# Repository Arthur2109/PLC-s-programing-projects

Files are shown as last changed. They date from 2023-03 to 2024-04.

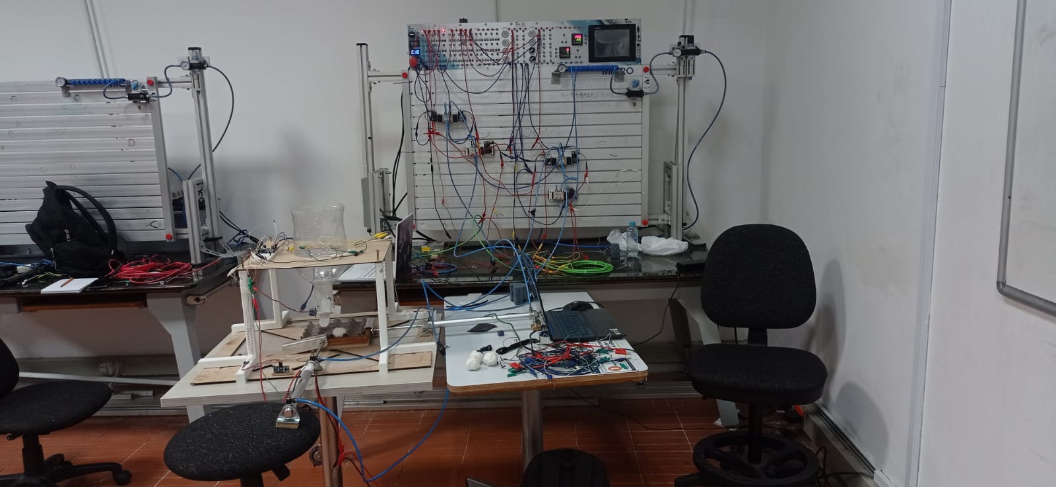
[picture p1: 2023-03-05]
projet-préhenseur-oeuf/photos-vidéos/systeme-entier.jpeg

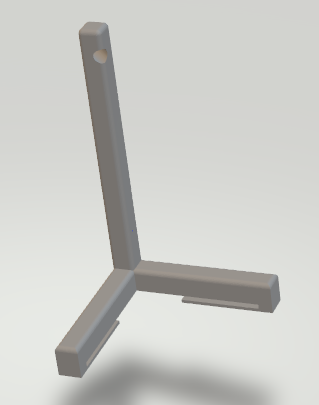
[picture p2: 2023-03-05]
projet-préhenseur-oeuf/trepied/trepied.png

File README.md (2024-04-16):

# PLC-s-programing-projects
PLC's programing projects coded in Ladder, Grafcet or FBD (function block diagram).

1) Projet préhenseur d'oeuf (codé en FDB): projet de plusieurs mois qui consiste a placer des oeufs dans une boite d'oeufs de maniere automatique.
Les oeufs sont a l'origine placés dans une bouteilles (cf photos et vidéos). Un tourniquet s'actionne pour laisser tomber un oeuf dans la boite. A chaque fois qu'un oeuf tombe pour occuper un espace de la boite, les pistons X et Y de déplacent d'un cran (asservissement de la position a l'aide de capteur ultrasons placés le long des axes X et Y, + structure en glissiere qui permet le mouvement independant X Y de la boite). Le parcours de tous les emplacements de la boite est ainsi fait qu'il permet de ne faire aucun aller retour pour ne pas perdre de temps (zig-zag).

Conception des pieces sous Inventor (AutoCAD).

Problemes de ce projet :
- Le capteur ultrason est adapté a un microcontroleur mais pas a un PLC (cf explication fichier arduino).
- La structure des glissieres crée un arc-boutement important et bloque le glissement (cf videos).
- Manque de temps significatif.

2) Grafcet : Petit programme de simulation de deux pistons et d'un moteur codé en Grafcet. Asservissement de la vitesse du moteur. A executer sous Automation Studio.

3) Ladder : Petit programme de simulation de deux pistons, codé en Ladder. le bouton ON actionne les pistons suivant la séquence X+,attente,X-,Y+,attente,Y-. A executer aussi sous Automation Studio.

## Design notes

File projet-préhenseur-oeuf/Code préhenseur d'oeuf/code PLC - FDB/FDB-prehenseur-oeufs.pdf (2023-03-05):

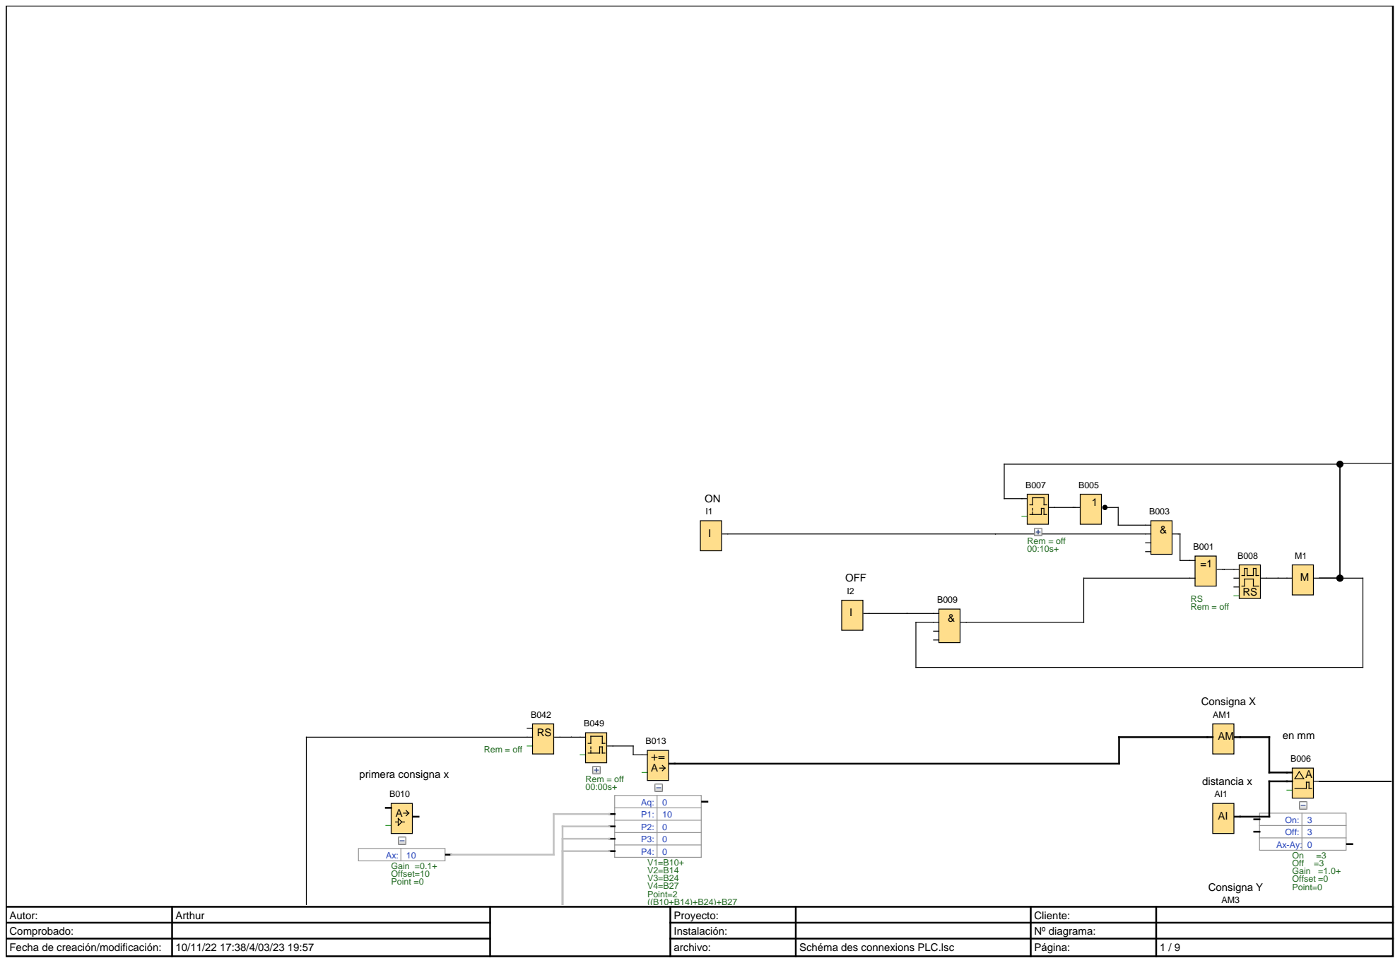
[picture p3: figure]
Autor:; Arthur; Proyecto:; Cliente:; Comprobado:; Instalación:; Nº diagrama:; Fecha de creación/modificación:; archivo:; Schéma des connexions PLC.lsc; OFF; distancia x; Consigna X; Rem = off 00:10s+; Off:; RSRem = off; Consigna Y; V1=B10+ V2=B14 V3=B24 V4=B27 Point=2; Gain =0.1+ Offset=10 Point =0; primera consigna x; Rem = off; Rem = off 00:00s+

On =3 Off =3 Gain =1.0+ Offset =0 Point=0

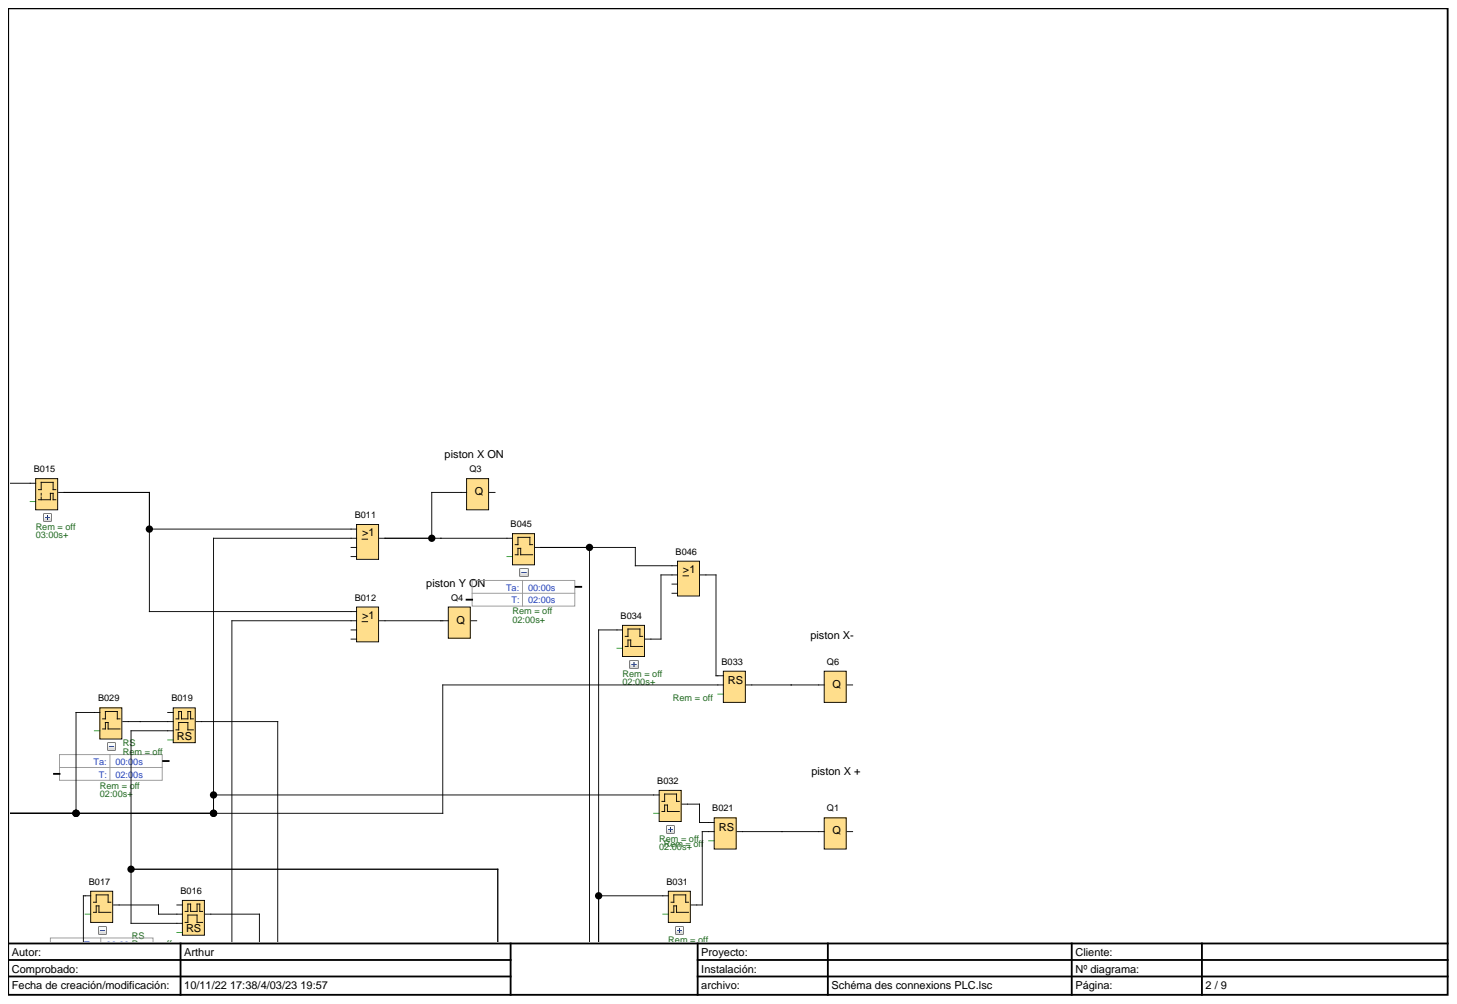
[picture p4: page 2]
piston X ON; piston Y ON; RSRem = off; Rem = off 02:00s+; piston X +; piston X-; Rem = off; Rem = off 03:00s+

Ta: | 00:00s
T: | 02:00s

Autor: | Arthur | Proyecto: | Cliente:

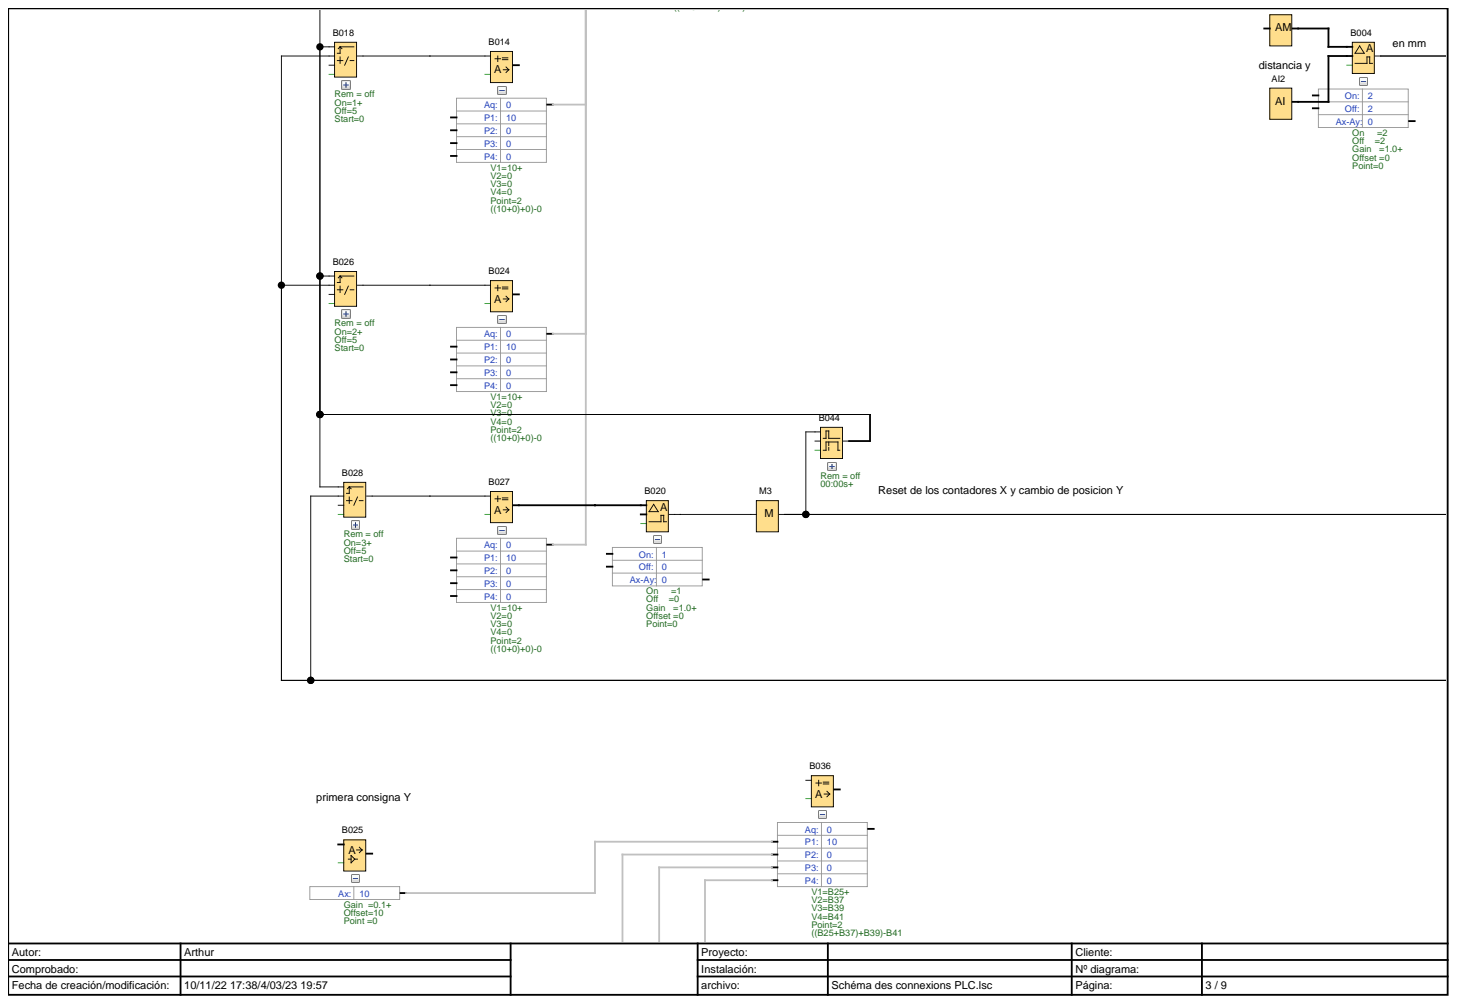
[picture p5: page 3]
Autor:; Arthur; Proyecto:; Cliente:; distancia y; Off:; V1=10+ V2=0 V3=0 V4=0 Point=2; Reset de los contadores X y cambio de posicion Y; primera consigna Y; V1=B25+ V2=B37 V3=B39 V4=B41 Point=2; Rem = off 00:00s+

Rem = off On=1+ Off=5 Start=0

On =2 Off =2 Gain =1.0+ Offset =0 Point=0

P2: | 0
P3: | 0
P4: | 0

Rem = off On=2+ Off=5 Start=0

Aq: | 0
P1: | 10

Rem = off On=3+ Off=5 Start=0

On =1 Off =0 Gain =1.0+ Offset =0 Point=0

Gain =0.1+ Offset=10 Point =0

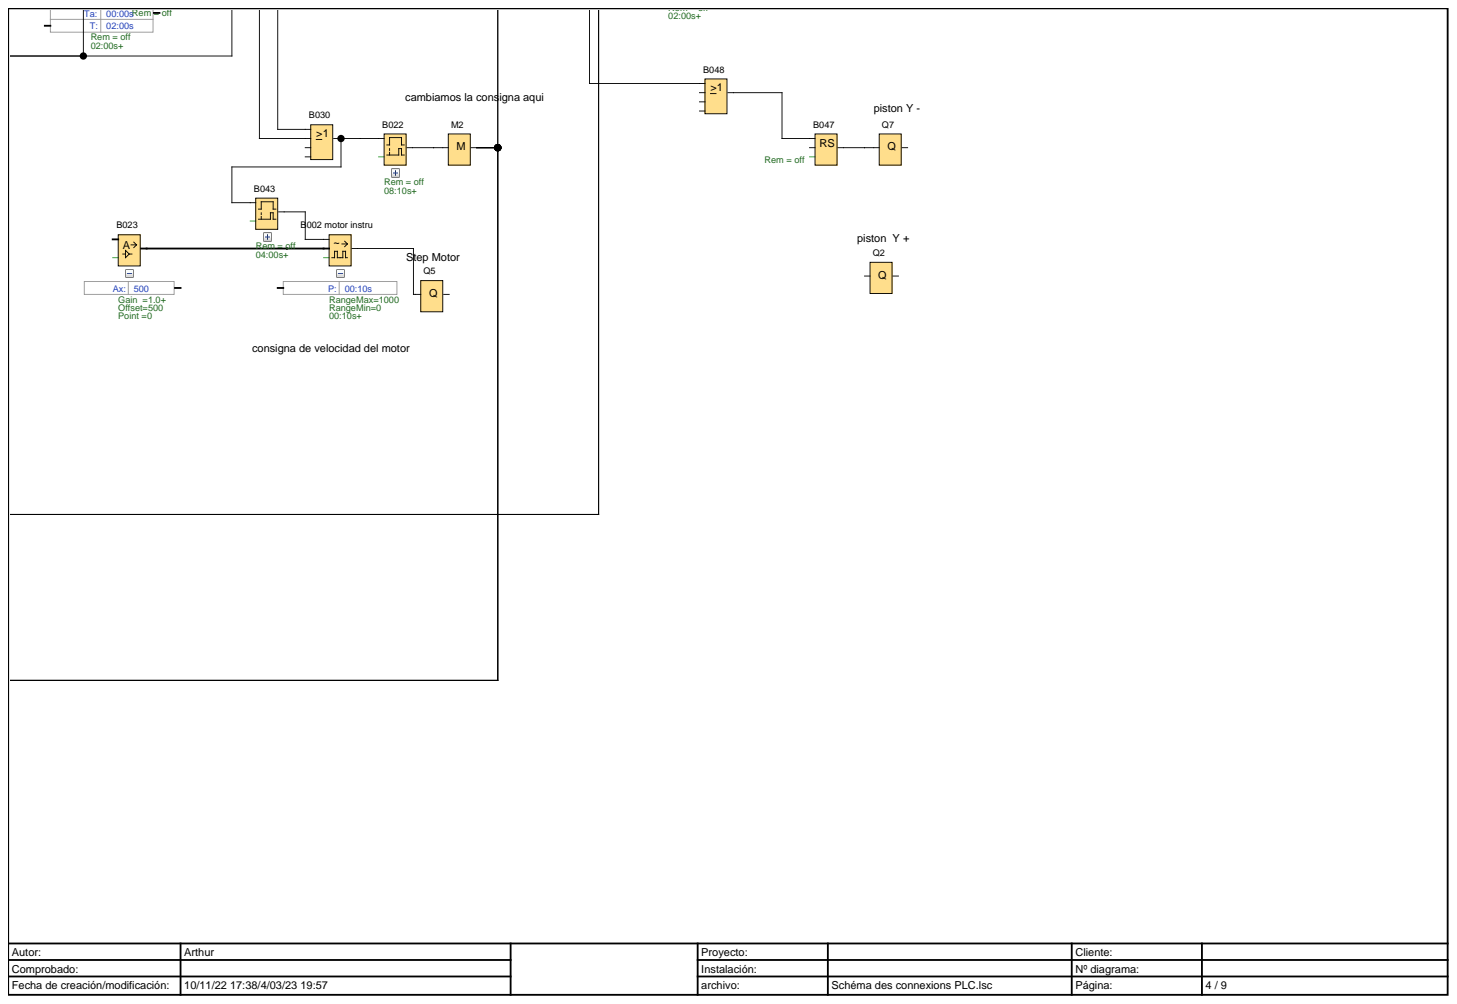
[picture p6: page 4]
Autor:; Arthur; Proyecto:; Cliente:; piston Y + ~; B002 motor instru; RangeMax=1000 RangeMin=0; Step Motor; Rem = off 08:10s+; piston Y -; Rem = off 02:00s+; Rem = off; Rem = off 04:00s+

Ta: | 00:00s Rem = off | B030 | 02:00s+ B048
T: | 02:00s

cambiamos la consigna aqui

Gain =1.0+ Offset=500 Point =0

consigna de velocidad del motor

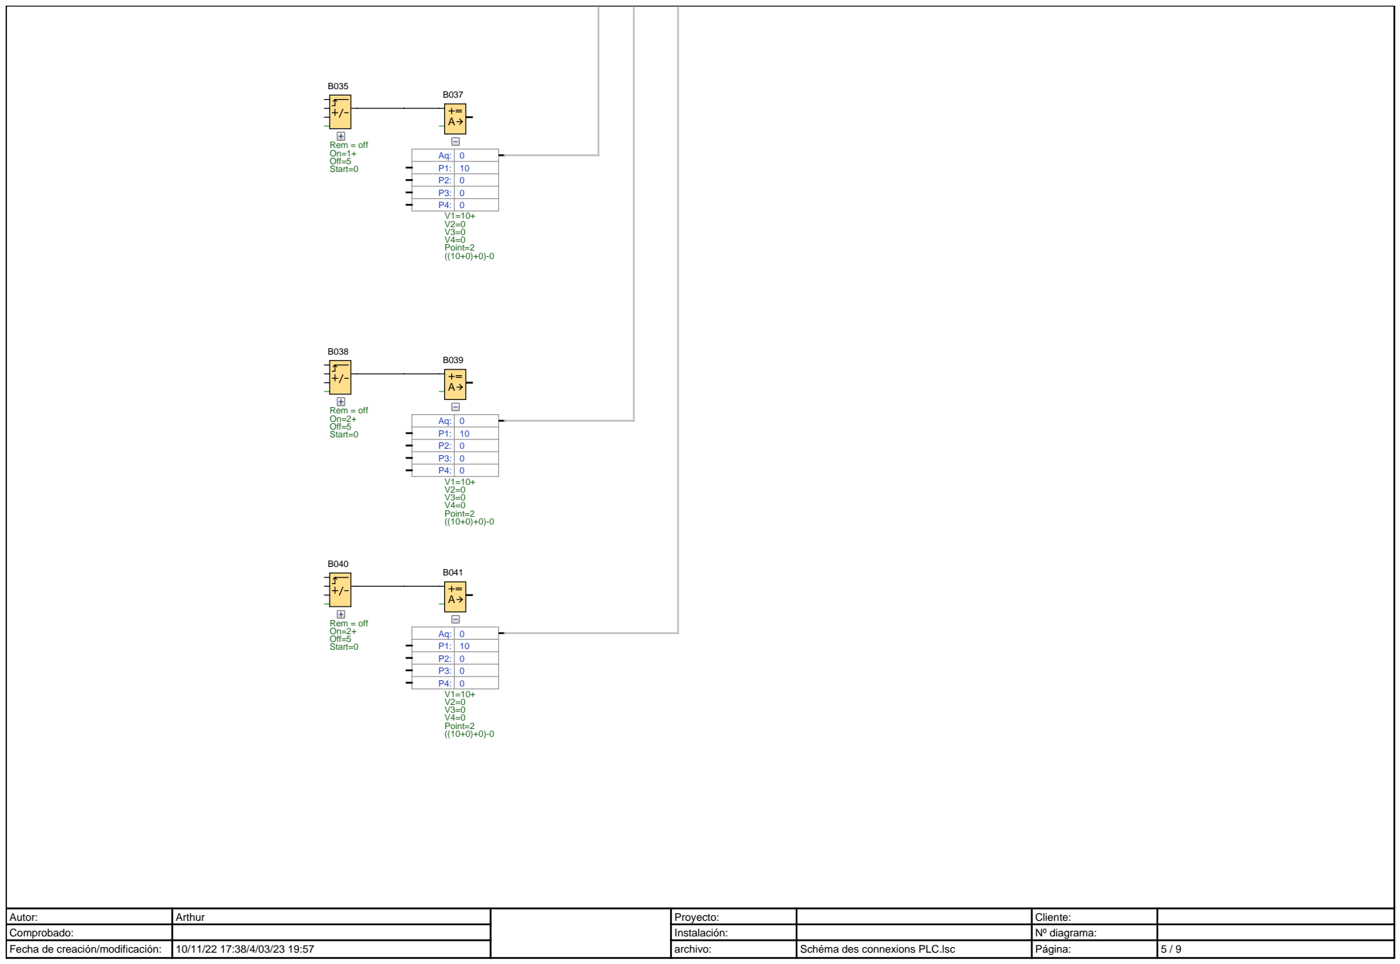
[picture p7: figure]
Autor:; Arthur; Proyecto:; Cliente:; Rem = off On=1+ Off=5 Start=0; V1=10+ V2=0 V3=0 V4=0 Point=2; Rem = off On=2+ Off=5 Start=0

Número de bloque (tipo) | Parámetro

AI1(Entrada analógica) : distancia x

AI2(Entrada analógica) : distancia y

AM1(Marca analógica) : Consigna X

AM3(Marca analógica) : Consigna Y

B002 motor instru(PWM) : | RangeMax=1000 RangeMin=0 00:10s+
B004(Comparador analógico) : | On =2 Off =2 Gain =1.0+ Offset =0 Point=0
B006(Comparador analógico) : | On =3 Off =3 Gain =1.0+ Offset =0 Point=0
B007(Retardo a la conexión) : | Rem = off 00:10s+
B008(Relé de impulsos) : | RS Rem = off
B010(Amplificador analógico) : | Gain =0.1+ Offset=10 Point =0
B013(Instrucción aritmética) : | V1=B10+ V2=B14 V3=B24 V4=B27 Point=2 ((B10+B14)+B24)+B27
B014(Instrucción aritmética) : | V1=10+ V2=0 V3=0 V4=0 Point=2 ((10+0)+0)-0
B015(Retardo a la conexión) : | Rem = off 03:00s+
B016(Relé de impulsos) : | RS Rem = off
B017(Relé de barrido (Salida de impulsos)) : | Rem = off 02:00s+
B018(Contador adelante/atrás) : | Rem = off On=1+ Off=5 Start=0
B019(Relé de impulsos) : | RS Rem = off
B020(Comparador analógico) : | On =1 Off =0 Gain =1.0+ Offset =0 Point=0
B021(Relé autoenclavador) : | Rem = off
B022(Retardo a la conexión) : | Rem = off 08:10s+
B023(Amplificador analógico) : | Gain =1.0+ Offset=500 Point =0
Autor: | Arthur

Proyecto:

Cliente:

Página:

Número de bloque (tipo) | Parámetro
B024(Instrucción aritmética) : | V1=10+ V2=0 V3=0 V4=0 Point=2 ((10+0)+0)-0
B025(Amplificador analógico) : | Gain =0.1+ Offset=10 Point =0
B026(Contador adelante/atrás) : | Rem = off On=2+ Off=5 Start=0
B027(Instrucción aritmética) : | V1=10+ V2=0 V3=0 V4=0 Point=2 ((10+0)+0)-0
B028(Contador adelante/atrás) : | Rem = off On=3+ Off=5 Start=0
B029(Relé de barrido (Salida de impulsos)) : | Rem = off 02:00s+
B031(Relé de barrido (Salida de impulsos)) : | Rem = off 02:00s+
B032(Relé de barrido (Salida de impulsos)) : | Rem = off 02:00s+
B033(Relé autoenclavador) : | Rem = off
B034(Relé de barrido (Salida de impulsos)) : | Rem = off 02:00s+
B035(Contador adelante/atrás) : | Rem = off On=1+ Off=5 Start=0
B036(Instrucción aritmética) : | V1=B25+ V2=B37 V3=B39 V4=B41 Point=2 ((B25+B37)+B39)-B41
B037(Instrucción aritmética) : | V1=10+ V2=0 V3=0 V4=0 Point=2 ((10+0)+0)-0
B038(Contador adelante/atrás) : | Rem = off On=2+ Off=5 Start=0
B039(Instrucción aritmética) : | V1=10+ V2=0 V3=0 V4=0 Point=2 ((10+0)+0)-0
B040(Contador adelante/atrás) : | Rem = off On=2+ Off=5 Start=0
B041(Instrucción aritmética) : | V1=10+ V2=0 V3=0 V4=0 Point=2 ((10+0)+0)-0
B042(Relé autoenclavador) : | Rem = off

Número de bloque (tipo) | Parámetro
B043(Retardo a la conexión) : | Rem = off 04:00s+
B044(Retardo a la desconexión) : | Rem = off 00:00s+
B045(Relé de barrido (Salida de impulsos)) : | Rem = off 02:00s+
B047(Relé autoenclavador) : | Rem = off
B049(Retardo a la conexión) : | Rem = off 00:00s+

I1(Entrada) : ON

I2(Entrada) : OFF

Q2(Salida) : piston Y +

Q3(Salida) : piston X ON

Q4(Salida) : piston Y ON

Q5(Salida) : Step Motor

Conector | Rotulación

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
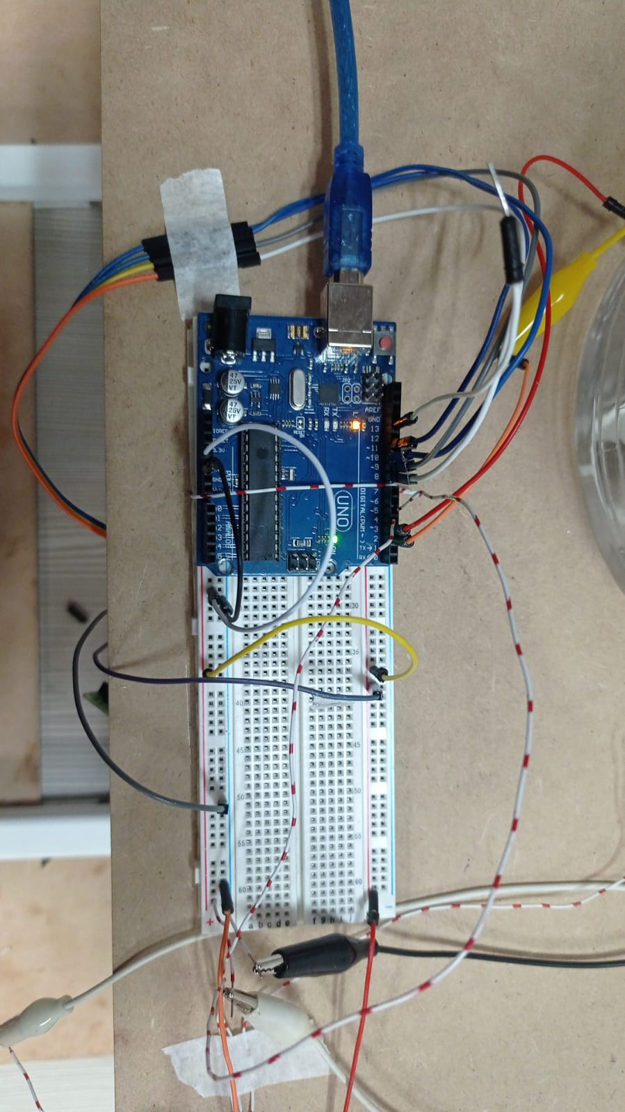
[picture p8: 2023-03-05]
projet-préhenseur-oeuf/photos-vidéos/zoom-arduino.jpeg

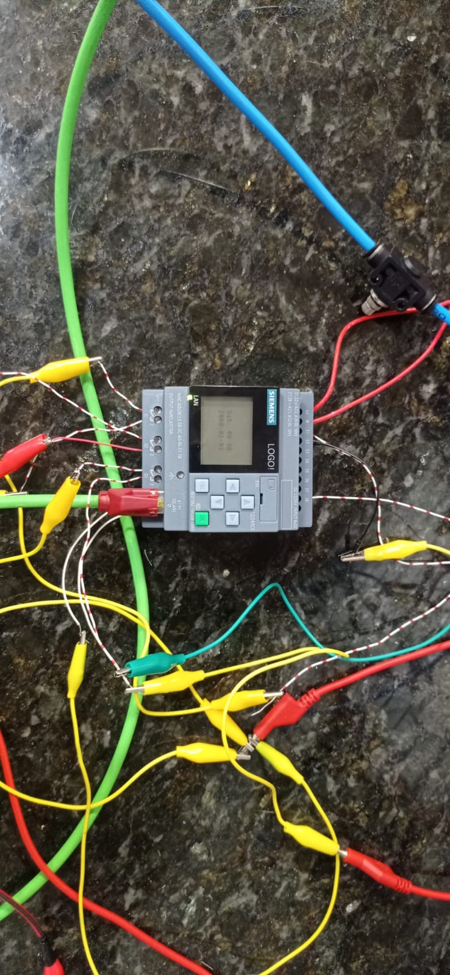
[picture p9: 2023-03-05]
projet-préhenseur-oeuf/photos-vidéos/zoom-PLC-connexion.jpeg

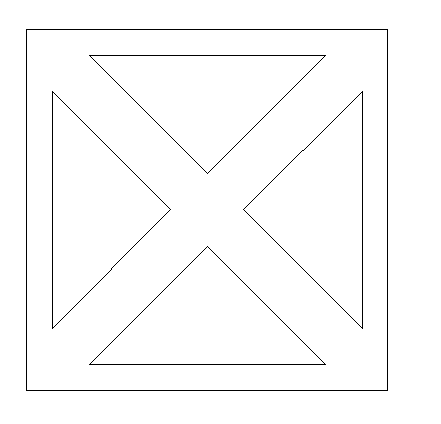
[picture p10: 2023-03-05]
projet-préhenseur-oeuf/base en bois aglo/base en algo.png

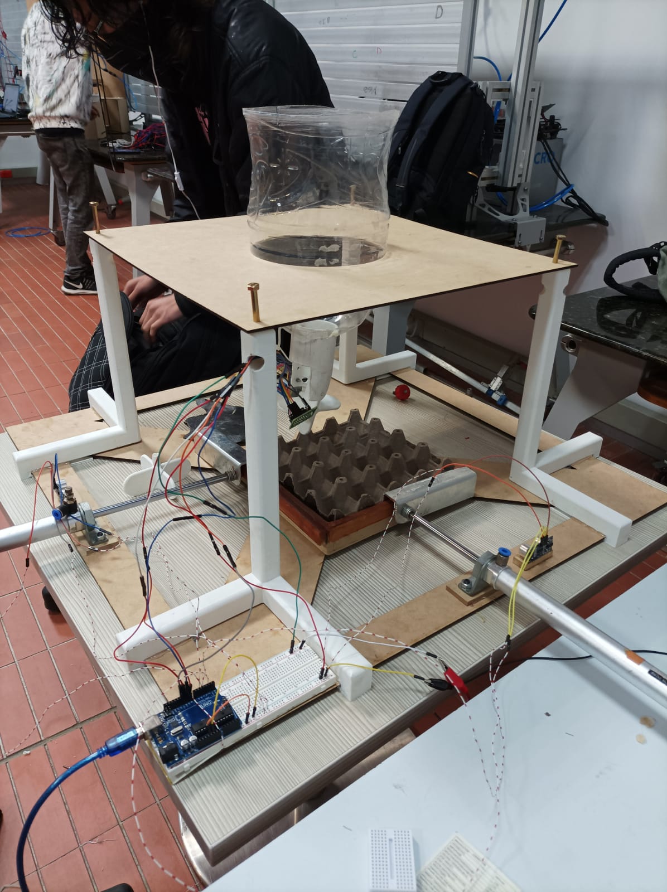
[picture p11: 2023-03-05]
projet-préhenseur-oeuf/photos-vidéos/strcuture-finale.jpeg

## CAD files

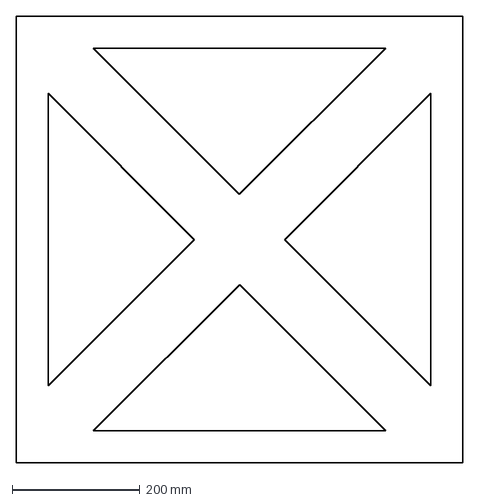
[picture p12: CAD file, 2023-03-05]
projet-préhenseur-oeuf/base en bois aglo/base.dxf
700.0 x 700.0 mm

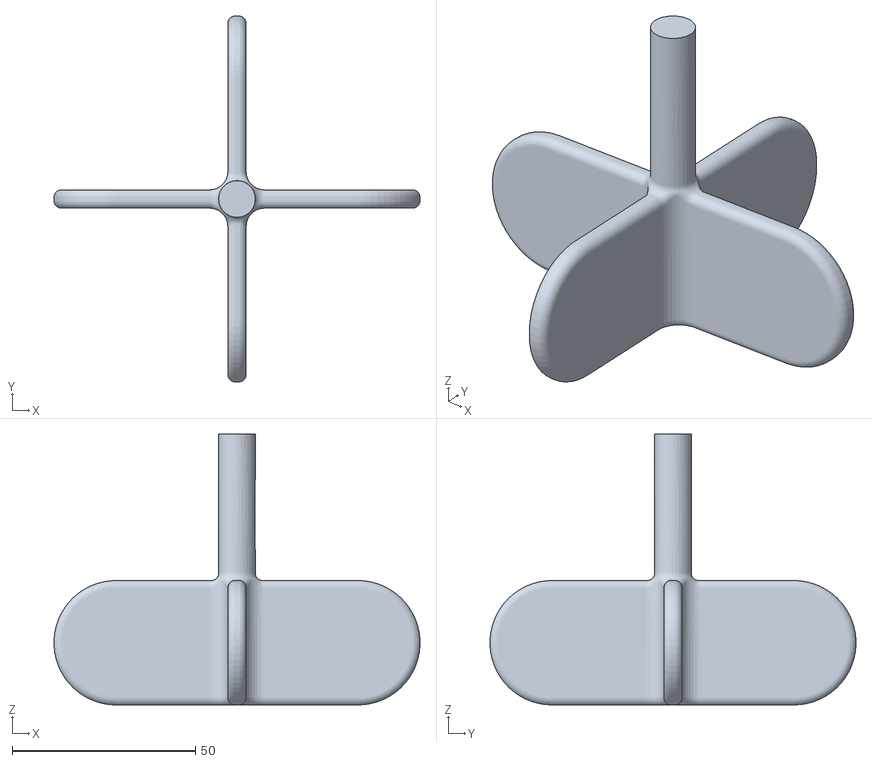
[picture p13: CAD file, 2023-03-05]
projet-préhenseur-oeuf/tourniquet/torniquete.stl
100.0 x 100.0 x 74.0

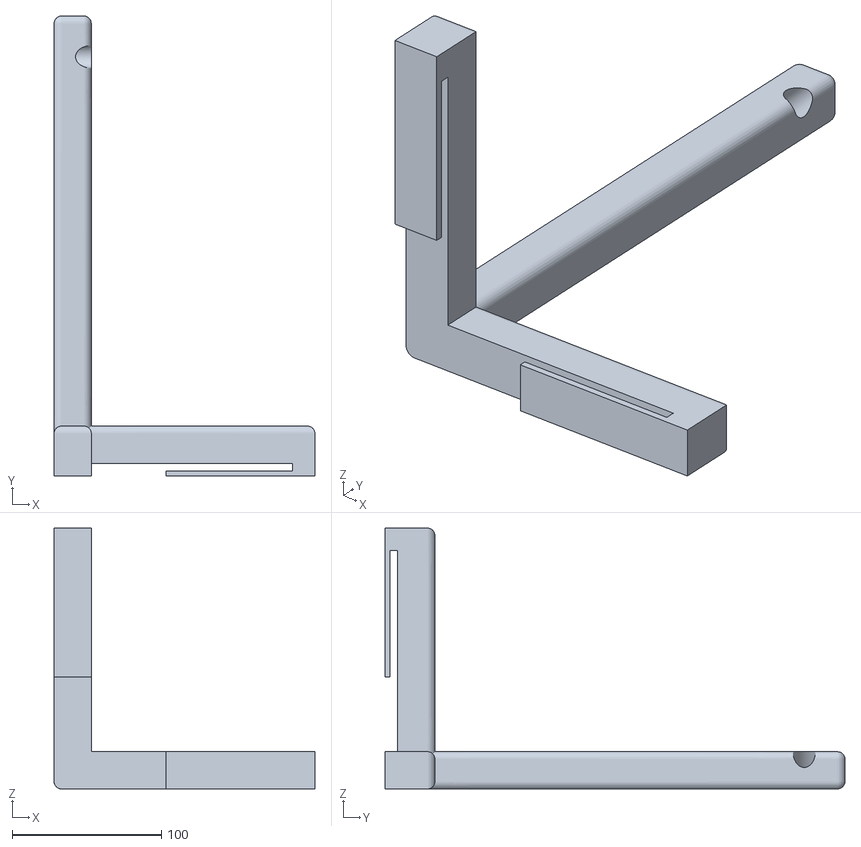
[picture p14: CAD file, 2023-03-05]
projet-préhenseur-oeuf/trepied/trepied.stl
175.0 x 308.5 x 175.0

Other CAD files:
projet-préhenseur-oeuf/base en bois aglo/base.ipt
projet-préhenseur-oeuf/tourniquet/torniquete.ipt
projet-préhenseur-oeuf/trepied/trepied.ipt

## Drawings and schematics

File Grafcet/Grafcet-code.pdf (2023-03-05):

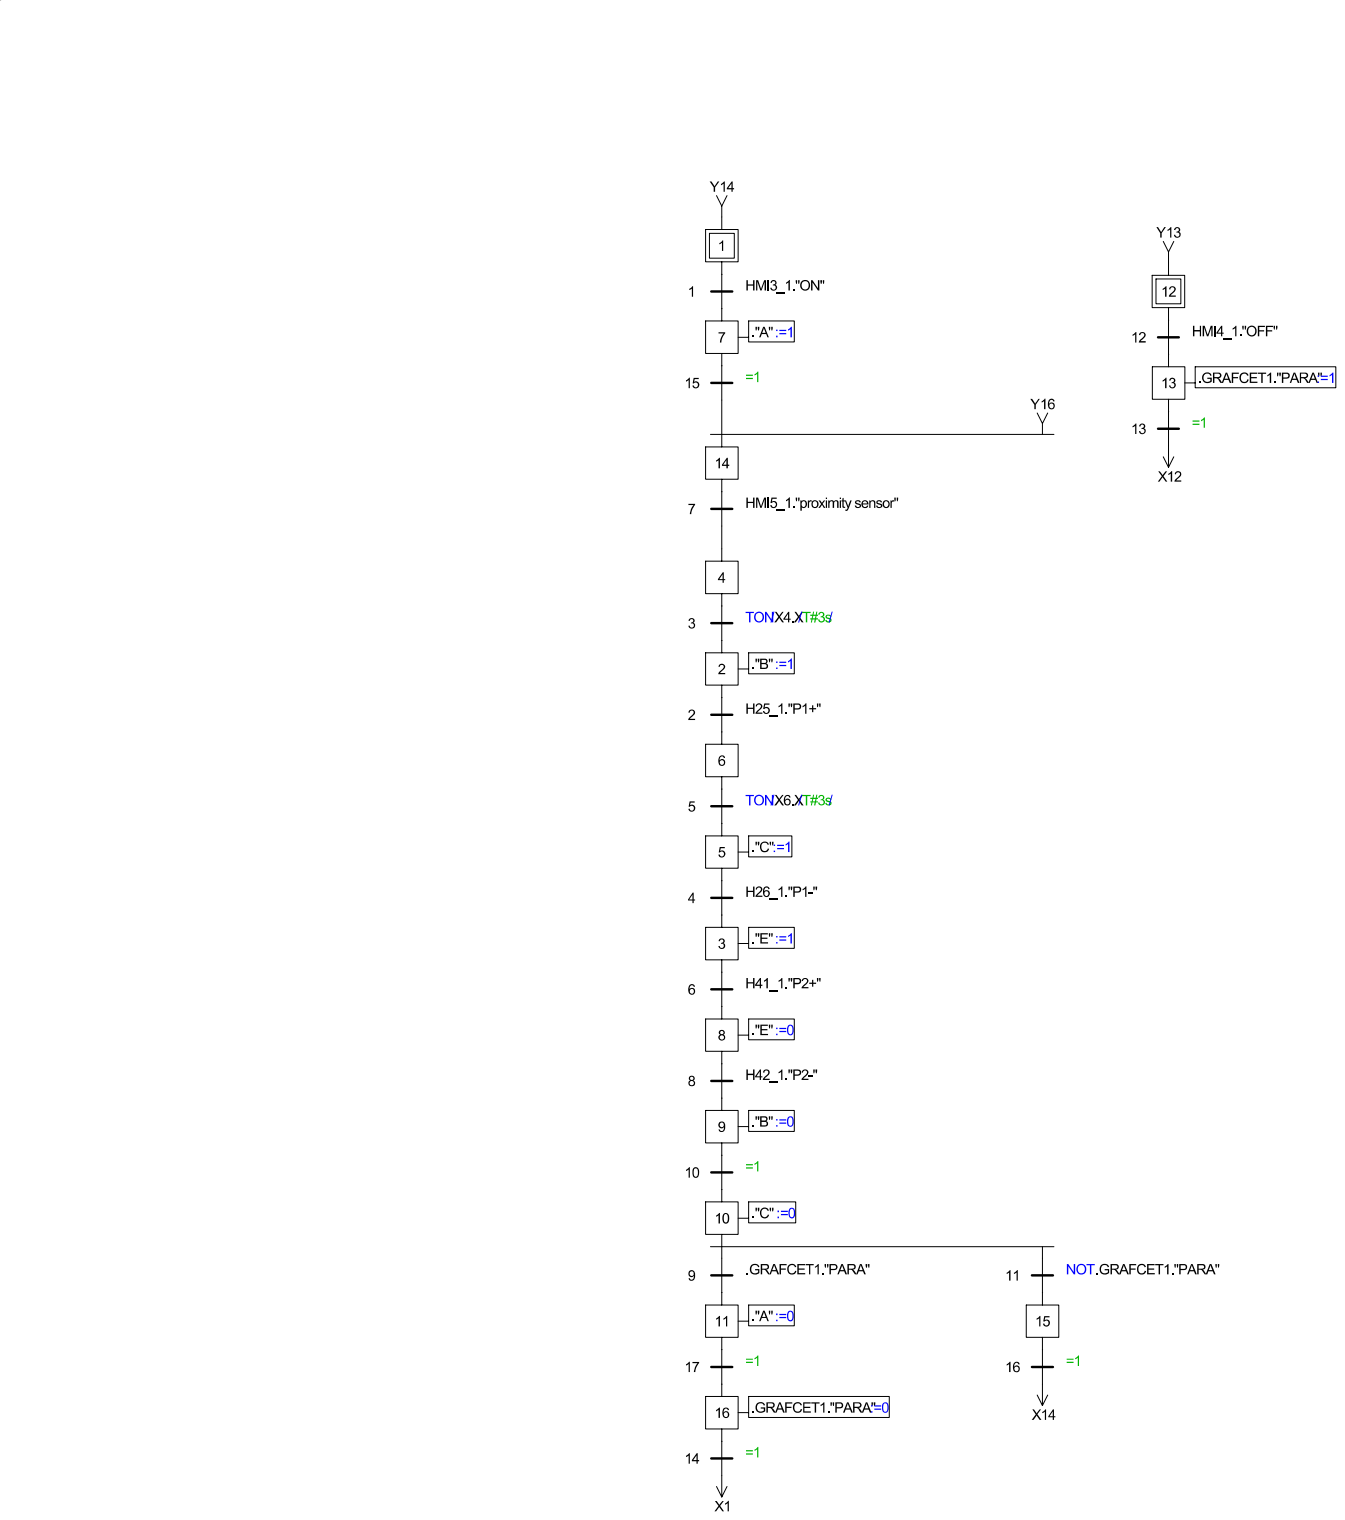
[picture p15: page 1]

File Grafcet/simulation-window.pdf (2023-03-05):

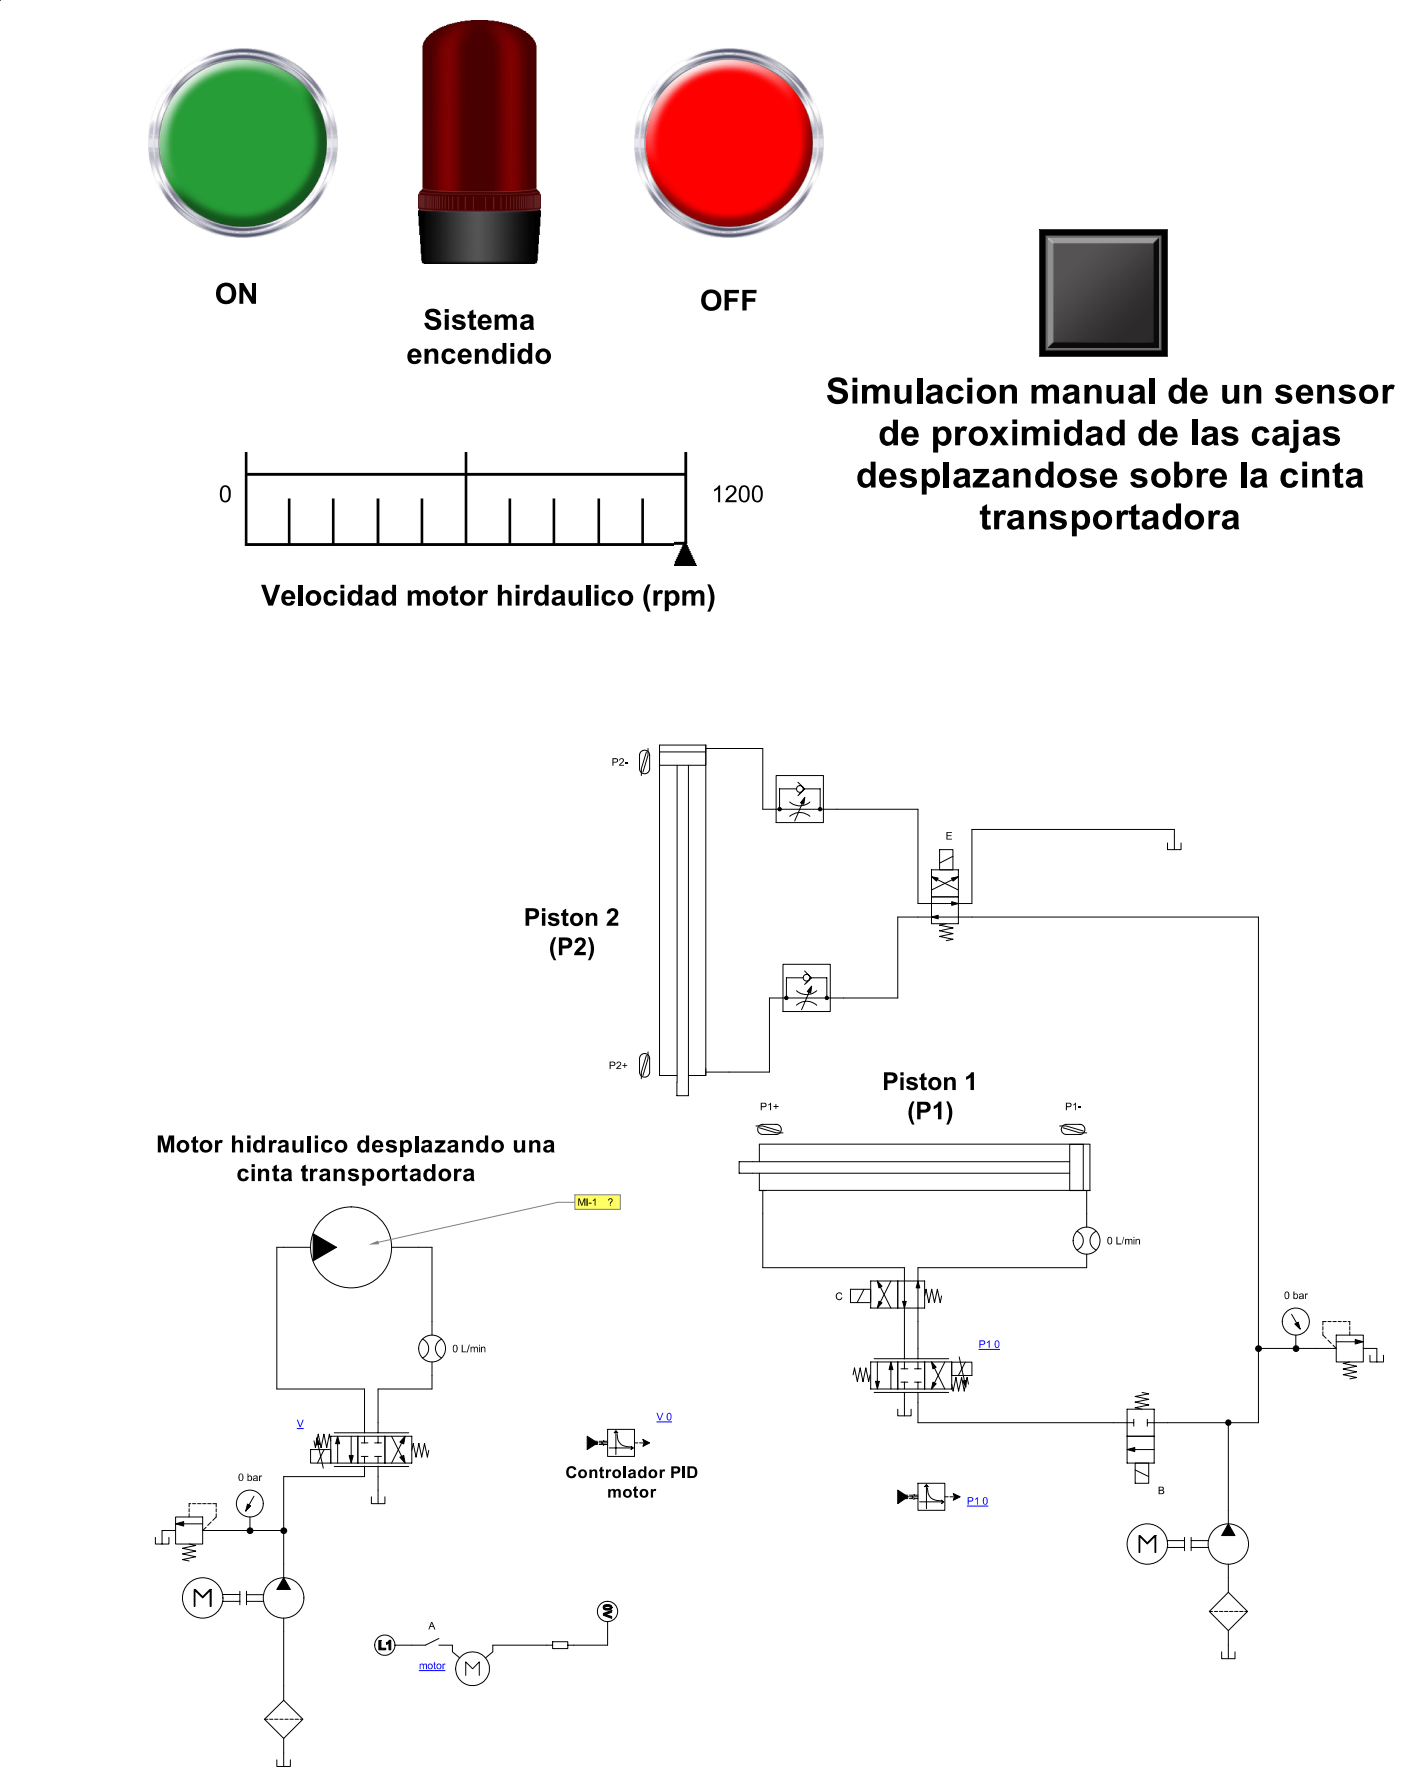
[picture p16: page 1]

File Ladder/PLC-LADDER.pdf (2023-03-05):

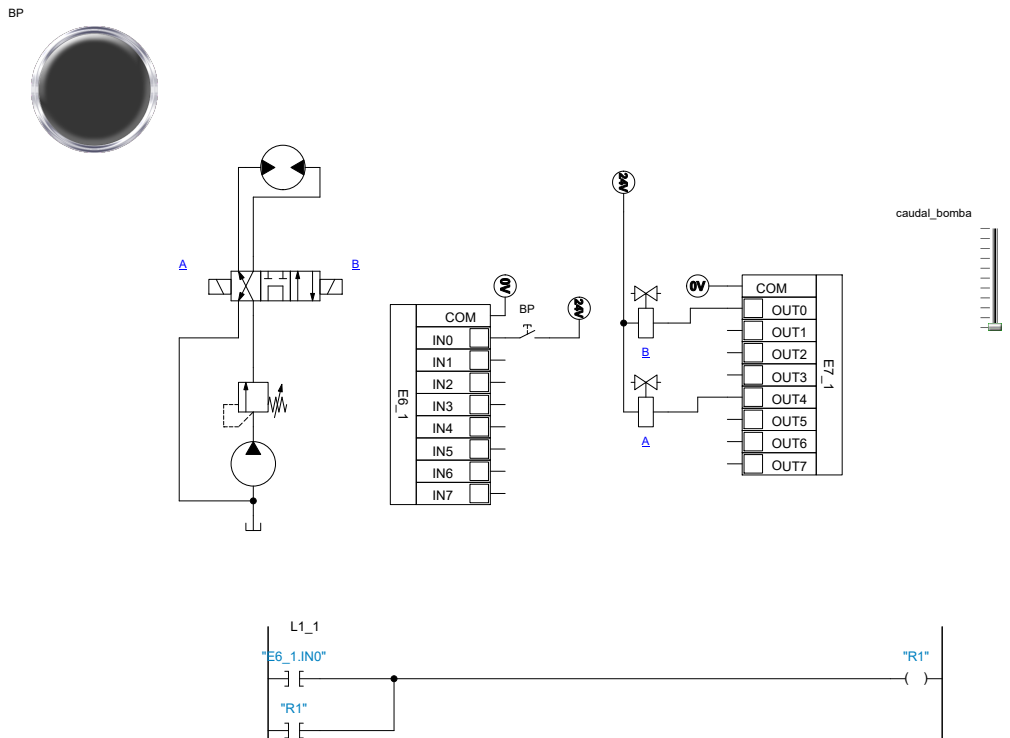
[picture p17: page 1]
BP A COM IN0 IN1 IN2 IN3 IN4 IN5; COMOUT0; OUT1 OUT2 OUT3 OUT4; OUT5; OUT6 OUT7 B; caudal_bomba

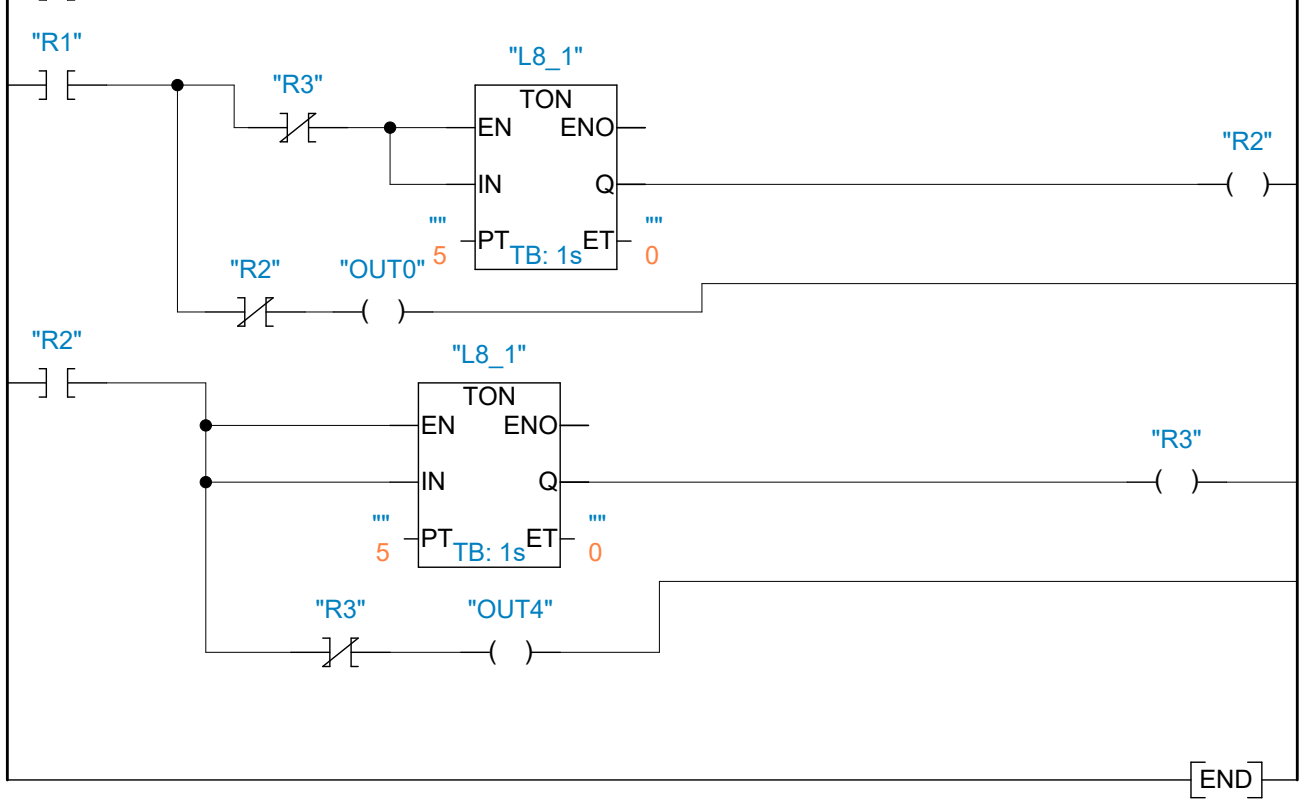
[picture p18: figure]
END; TON; ENOQ; "OUT0"; "OUT4"

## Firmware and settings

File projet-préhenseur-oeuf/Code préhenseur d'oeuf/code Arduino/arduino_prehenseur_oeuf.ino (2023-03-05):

// Nous ne pouvons pas nous passer d'arduino dans ce projet car le capteur de distance (ultrasons) nécessite une fréquence
// d'alimentation qui est supérieure a la fréquence d'ouverture et de fermeture du relais de sortie du PLC.
// Ce code a pour but de mesurer la distance qui sépare la structure du piston de la boite d'oeufs a l'aide
// d'un capteur ultrason, et envoie ensuite l'information au PLC. Il a aussi pour but de tourner le tourniquet quand il 
// en recoit l'ordre de la part du PLC.


#include <Stepper.h>
int stepsPerRevolution = 2048;
int motSpeed = 12;
int Trig_X=2;
int Echo_X=3;
int Trig_Y=4;
int Echo_Y=5;
int input_motor=6;
int tiempo_X;
int tiempo_Y;
int salida_X=12;
int salida_Y=13;
int X_map;
int Y_map;

Stepper myStepper(stepsPerRevolution,8,10,9,11);



void setup() {
  pinMode(salida_X,OUTPUT);
  pinMode(salida_Y,OUTPUT);
  pinMode(Trig_X,OUTPUT);
  digitalWrite(Trig_X,LOW);
  pinMode(Echo_X,INPUT);
  pinMode(input_motor,INPUT);
  Serial.begin(9600);
  myStepper.setSpeed(motSpeed);
  pinMode(Trig_Y,OUTPUT);
  digitalWrite(Trig_Y,LOW);
  pinMode(Echo_Y,INPUT);
}
  
   
//725 x mini
//1660 x maxi
// 420 min Y
// 1230 max Y



void loop() {
  digitalWrite(Trig_X,HIGH);
  delay(1);
  digitalWrite(Trig_X, LOW);
  tiempo_X=pulseIn(Echo_X,HIGH);
  digitalWrite(Trig_Y,HIGH);
  delay(1);
  digitalWrite(Trig_Y, LOW);
  tiempo_Y=pulseIn(Echo_Y,HIGH);
  Serial.println(tiempo_X);
  delay(50);
  X_map=map(tiempo_X,725,1660,0,255);
  Y_map=map(tiempo_Y,420,1230,0,255);
  analogWrite(salida_X,X_map);
  analogWrite(salida_Y,Y_map);

 if (digitalRead(input_motor==HIGH)){
  myStepper.step(-512);
  delay(500);
 }
}
 
